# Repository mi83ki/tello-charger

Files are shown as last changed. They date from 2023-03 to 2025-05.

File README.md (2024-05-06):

<!-- omit in toc -->
# Tello Charger

小型ドローンTelloの自動充電を可能にする装置です。

<!-- omit in toc -->
## 目次

- [1. Tello Chargerとは](#1-tello-chargerとは)
- [2. 製作するために必要なデータ](#2-製作するために必要なデータ)
  - [2.1. 3Dデータ](#21-3dデータ)
  - [2.2. 回路図](#22-回路図)
  - [2.3. ソースコード](#23-ソースコード)
    - [2.3.1. 開発環境の構築](#231-開発環境の構築)
      - [2.3.1.1. VSCodeのインストール](#2311-vscodeのインストール)
      - [2.3.1.2. PlatformIOのインストール](#2312-platformioのインストール)
    - [2.3.2. 初期設定](#232-初期設定)
      - [2.3.2.1. サブモジュールの取得](#2321-サブモジュールの取得)
      - [2.3.2.2. ssid.hの作成](#2322-ssidhの作成)
    - [2.3.3. ソフトウェアの書き込み](#233-ソフトウェアの書き込み)
      - [2.3.3.1. ワークスペースを開く](#2331-ワークスペースを開く)
      - [2.3.3.2. ビルド](#2332-ビルド)
      - [2.3.3.3. 書き込み](#2333-書き込み)
- [3. WebAPI仕様](#3-webapi仕様)
- [4. 概要設計書](#4-概要設計書)

## 1. Tello Chargerとは

Tello EDUの自動充電装置です。

以下はドローンにUSBコネクタを接続する機構の動画です。

ドローンキャッチ (https://youtube.com/shorts/hyMHSOp_BFY)

以下はドローンを自動充電する一連動作の動画です。

ドローン着陸 (https://youtube.com/shorts/O7KXj6DnHRI)

## 2. 製作するために必要なデータ

製作するために必要なデータを以下に説明します。

### 2.1. 3Dデータ

3Dデータ（STEP）は`step/`ディレクトリに保存しています。\
STLデータ等に変換し、3Dプリンタで印刷します。\
3Dデータの品番リストは[概要設計書](doc/design/design.md)を参照してください。

### 2.2. 回路図

回路図（Eegleデータ）は`eagle/`ディレクトリに保存しています。\
必要な部品を購入し、ユニバーサル基板で手はんだします。\
必要な部品のリストは[概要設計書](doc/design/design.md)を参照してください。

### 2.3. ソースコード

ATOM Liteに書き込むソースコードは`src/`ディレクトリに保存しています。

#### 2.3.1. 開発環境の構築

##### 2.3.1.1. VSCodeのインストール

Arduinoマイコンへの書き込みも可能なエディタとしてVSCodeを推奨する。\
以下のURLに従ってVSCodeをインストールする。\
<https://miya-system-works.com/blog/detail/vscode-install/>

##### 2.3.1.2. PlatformIOのインストール

以下URLを参考に、VSCodeの拡張機能であるPlatformIOをインストールする。\
<https://zenn.dev/kotaproj/articles/esp32_vscode_pio>

#### 2.3.2. 初期設定

初回に必要な作業を記載します。

##### 2.3.2.1. サブモジュールの取得

以下のコマンドでサブモジュールを取得する必要があります。

~~~bash
git submodule update --init
~~~

##### 2.3.2.2. ssid.hの作成

WiFiの接続先SSIDとパスワードは以下の手順で設定します。

1. 「src/TelloCharger/src/」フォルダの「ssid_example.h」を同じフォルダにコピーして「ssid.h」に名称変更する

2. 「ssid.h」の各項目を自分の環境に合わせて変更する

    ~~~h
    /**
     * @file ssid_example.h
     * @brief SSID情報を記述するヘッダファイルの例
     *
     * @details 環境に合わせて、ファイル名をssid.hにリネームして利用してください（ssid.hはgitignoreされている）
     */

    #pragma once

    #define WIFI_SSID "XXXXXXXXXXX"
    #define WIFI_PASSWORD "XXXXXXXX"

    /** 固定IPアドレス（"MY_FIXED_IP_1"."MY_FIXED_IP_2"."MY_FIXED_IP_3"."MY_FIXED_IP_4"） */
    #define MY_FIXED_IP_1 (192)
    #define MY_FIXED_IP_2 (168)
    #define MY_FIXED_IP_3 (1)
    #define MY_FIXED_IP_4 (12)

    /** ゲートウェイのIPアドレス（"MY_FIXED_IP_1"."MY_FIXED_IP_2"."MY_FIXED_IP_3"."GATEWAY_IP_4"） */
    #define GATEWAY_IP_4 (1)
    ~~~

#### 2.3.3. ソフトウェアの書き込み

##### 2.3.3.1. ワークスペースを開く

「xsa-cloud/xsa-cloud.code-workspace」をダブルクリックしてVSCodeで開く。

##### 2.3.3.2. ビルド

左下の`✓`ボタンを押下する。

##### 2.3.3.3. 書き込み

クナイデバイスをUSBケーブルでPCに接続し、左下の`→`ボタンを押下する。

## 3. WebAPI仕様

TelloChargerは上位システムからWebAPIで制御します。\
以下のAPI仕様を参照してください。

[Tello Charger API](doc/openapi/api.html)

## 4. 概要設計書

概要設計内容は以下を参照してください。

[概要設計書](doc/design/design.md)

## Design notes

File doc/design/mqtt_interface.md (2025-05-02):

<!-- omit in toc -->
# MQTT通信仕様書

<!-- omit in toc -->
## 改訂履歴

| 日付 | 版 | 変更者 | 変更内容 |
|---|----|---|---|
| 2025/5/2 | 0.1.0 | Miyazaki | 初版作成 |

<!-- omit in toc -->
## 目次

- [1. 目的](#1-目的)
- [2. システム全体概要](#2-システム全体概要)
- [3. ブローカー設定](#3-ブローカー設定)
- [4. トピック定義](#4-トピック定義)
- [5. ペイロード仕様](#5-ペイロード仕様)
  - [5.1. 共通ヘッダー (要求/応答系)](#51-共通ヘッダー-要求応答系)
  - [5.2. `ChargeStatusPayload`](#52-chargestatuspayload)
  - [5.3. `ChargeStartRequestPayload`](#53-chargestartrequestpayload)
  - [5.4. `ChargeStartResponsePayload`](#54-chargestartresponsepayload)
  - [5.5. `ChargeStopRequestPayload`](#55-chargestoprequestpayload)
  - [5.6. `ChargeStopResponsePayload`](#56-chargestopresponsepayload)
  - [5.7. `PowerOnRequestPayload`](#57-poweronrequestpayload)
  - [5.8. `PowerOnResponsePayload`](#58-poweronresponsepayload)

---

## 1. 目的

このドキュメントは、システム内で使用する **MQTT 通信** の仕様を統一し、開発者・運用者間で共通理解を得ることを目的とします。

---

## 2. システム全体概要

MQTT

---

## 3. ブローカー設定

| 項目 | 値 | 備考 |
|---|----|---|
| ホスト名 | `XX.XX.XX.XX` | MQTTブローカーのホスト |
| ポート | `1883` | — |
| プロトコル | MQTT v3.1 | — |

---

## 4. トピック定義

> `{device_id}` は実際のデバイス ID に置換して利用してください。

| トピック | 方向<br>(Pub/Sub) | QoS | Retain | Payloadスキーマ | 説明 |
|---|:---:|:---:|:---:|---|---|
| `drone-charger/{device_id}/charge/status` | Pub | 1 | No | `ChargeStatusPayload` | 充電状態の定期通知 |
| `drone-charger/{device_id}/charge/start/request` | Sub | 1 | No | `ChargeStartRequestPayload` | 充電開始要求 |
| `drone-charger/{device_id}/charge/start/response` | Pub | 1 | No | `ChargeStartResponsePayload` | 充電開始応答 |
| `drone-charger/{device_id}/charge/stop/request` | Sub | 1 | No | `ChargeStopRequestPayload` | 充電停止要求 |
| `drone-charger/{device_id}/charge/stop/response` | Pub | 1 | No | `ChargeStopResponsePayload` | 充電停止応答 |
| `drone-charger/{device_id}/power/on/request` | Sub | 1 | No | `PowerOnRequestPayload` | 電源ON要求 |
| `drone-charger/{device_id}/power/on/response` | Pub | 1 | No | `PowerOnResponsePayload` | 電源ON応答 |

---

## 5. ペイロード仕様

### 5.1. 共通ヘッダー (要求/応答系)

| フィールド | 型 | 必須 | 説明 |
|---|----|:----:|---|
| `timestamp` | string (ISO 8601) | Yes | 送信日時 (UTC) |
| `req_id` | string (UUIDv4) | Yes | 要求一意識別子 |
| `status` | string | Yes | 処理結果 (`SUCCESS`, `FAILURE` など) |
| `error` | string | No | エラー詳細 (成功時は空文字) |

### 5.2. `ChargeStatusPayload`

```json
{
  "charge": true,
  "current": 0,
  "chargingTime": 0,
  "isStartChargeExecuting": true,
  "isStopChargeExecuting": true,
  "isPowerOnExecuting": true
}
```

| フィールド | 型 | 必須 | 説明 |
|---|----|:----:|---|
| `charge` | boolean | Yes | 充電中かどうか (`true` = 充電中) |
| `current` | number | Yes | 充電電流 (mA) |
| `chargingTime` | number | Yes | 充電経過時間 (秒) |
| `isStartChargeExecuting` | boolean | Yes | 充電開始処理が実行中か |
| `isStopChargeExecuting` | boolean | Yes | 充電停止処理が実行中か |
| `isPowerOnExecuting` | boolean | Yes | 電源ON処理が実行中か |

### 5.3. `ChargeStartRequestPayload`

```json
{
  "timestamp": "2025-05-02T11:00:00Z",
  "req_id": "550e8400-e29b-41d4-a716-446655440000"
}
```

### 5.4. `ChargeStartResponsePayload`

```json
{
  "req_id": "550e8400-e29b-41d4-a716-446655440000",
  "status": "SUCCESS",
  "error": ""
}
```

### 5.5. `ChargeStopRequestPayload`

```json
{
  "timestamp": "2025-05-02T11:05:00Z",
  "req_id": "3fa85f64-5717-4562-b3fc-2c963f66afa6"
}
```

### 5.6. `ChargeStopResponsePayload`

```json
{
  "req_id": "3fa85f64-5717-4562-b3fc-2c963f66afa6",
  "status": "SUCCESS",
  "error": ""
}
```

### 5.7. `PowerOnRequestPayload`

```json
{
  "timestamp": "2025-05-02T11:10:00Z",
  "req_id": "1c16f6e0-6737-4d62-8c06-9f9fbc2384d8"
}
```

### 5.8. `PowerOnResponsePayload`

```json
{
  "req_id": "1c16f6e0-6737-4d62-8c06-9f9fbc2384d8",
  "status": "SUCCESS",
  "error": ""
}
```

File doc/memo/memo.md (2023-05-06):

<!-- omit in toc -->
# ドローン制御システム自由研究

## 1. 自動充電

### 1.1. Fusion360で平歯車の作成

ツール⇒アドイン⇒スクリプトとアドイン⇒Spur Gear（下側）
https://www.fact-cam.co.jp/product/2019/10/fusion360/archives/000447.html

## 2. GPS

### 2.1. telloにtileを付けた事例

https://www.thingiverse.com/thing:2943670
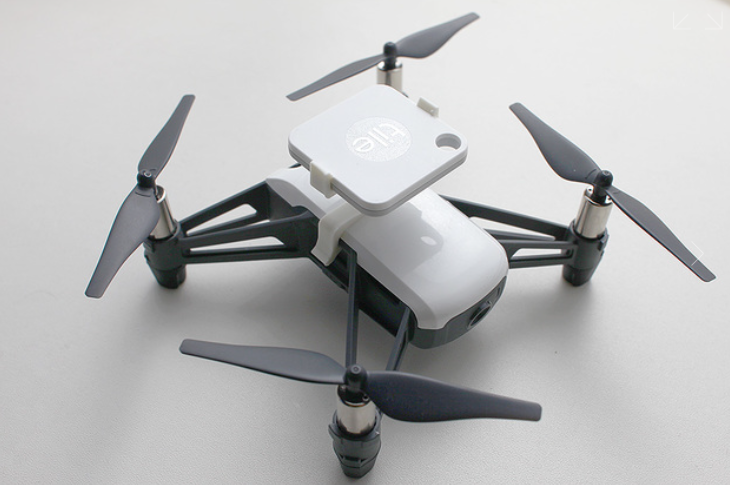
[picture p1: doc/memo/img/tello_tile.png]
tello_tile


## 3. センサ追加

| 品名 | 価格 | URL |
| --- | ---- | --- |
| TVOC/eCO2 ガスセンサユニット（SGP30） | 1606 | https://www.switch-science.com/products/6619 |
| M5Stack用 温湿度CO2センサ（SCD41） | 7117 | https://www.switch-science.com/products/8668 |
| ATOM Motionキット モーター/サーボドライバ（STM32F0搭載） | 3553 | https://www.switch-science.com/products/6993 |
| ATOMS3 Lite | 1386 | https://www.switch-science.com/products/8778 |

## 4. PlatformIOを使ってみる

### 4.1. PlatformIOのインストール

以下のURLを参考にPlatformIOをインストールします。\
<https://takabus.com/tips/2402/>

1. VSCodeをインストールする
1. PlatformIOの拡張機能をインストールする
1. プロジェクトを新規作成する
1. 今回はATOM Liteを使用するため、Bord: M5Stack-ATOM を選択する

### 4.2. ライブラリのインストール

PlatformIOのLibrariesから以下をインストールする

1. M5Atom
1. FastLED

## 5. サンプルプログラムの実行

以下のLチカプログラムを実行する

~~~cpp
#include <M5Atom.h> //Atomのヘッダファイルを準備
//FastLED（CRGB構造体）設定
CRGB dispColor(uint8_t r, uint8_t g, uint8_t b) {
  return (CRGB)((r << 16) | (g << 8) | b);
}
// 初期設定 -----------------------------------------------
void setup() {
  // 本体初期化（UART有効, I2C無効, LED有効
  M5.begin(true, false, true);
  // LED全消灯（赤, 緑, 青)
  M5.dis.drawpix(0, dispColor(0, 0, 0));
}
// メイン -------------------------------------------------
void loop() {
  M5.update(); //本体のボタン状態更新
  if (M5.Btn.isPressed()) {  //ボタンが押されていれば
    M5.dis.drawpix(0, dispColor(0, 0, 255)); //LED（指定色）
  } else { //ボタンが押されてなければ
    M5.dis.drawpix(0, dispColor(20, 20, 20)); //LED（白）
  }
  delay(100); //100ms待機
}
~~~

## 6. 自作ライブラリの取り込み

~~~bash
cd src/TelloCharger/lib/
git submodule add https://github.com/mi83ki/ArduinoCommon.git
~~~

## 7. WebAPIサーバーにする

参考にしたURL
<https://qiita.com/poruruba/items/0e539875ecfbdbfb23db>

### 7.1. ライブラリのインストール

以下のライブラリインストールする

- bblanchon/ArduinoJson@^6.21.2
- ottowinter/ESPAsyncWebServer-esphome@^3.0.0

### 7.2. サンプルプログラムの実行

~~~cpp
#include <ArduinoJson.h>
#include <AsyncJson.h>
#include <AsyncTCP.h>
#include <ESPAsyncWebServer.h>
#include <M5Atom.h>

const char *wifi_ssid = "Your SSID";
const char *wifi_password = "Your Password";

#define HTTP_PORT 80
#define FORMAT_SPIFFS_IF_FAILED true
#define BUFFER_SIZE 30 * 1024
unsigned char buffer[BUFFER_SIZE];

AsyncWebServer server(HTTP_PORT);

void wifi_connect(const char *ssid, const char *password);

void notFound(AsyncWebServerRequest *request) {
  if (request->method() == HTTP_OPTIONS) {
    request->send(200);
  } else {
    request->send(404);
  }
}

void setup() {
  Serial.begin(115200);

  wifi_connect(wifi_ssid, wifi_password);

  server.on("/get", HTTP_GET, [](AsyncWebServerRequest *request) {
    AsyncWebParameter *p = request->getParam("download");
    if (p != NULL)
      Serial.println(p->value());

    request->send(200, "text/plain", "Hello, world");
  });

  AsyncCallbackJsonWebHandler *handler = new AsyncCallbackJsonWebHandler(
      "/post", [](AsyncWebServerRequest *request, JsonVariant &json) {
        JsonObject jsonObj = json.as<JsonObject>();
        int p1 = jsonObj["p1"] | -1;

        const char *p_param = jsonObj["param"];
        if (p_param != NULL) {
          Serial.println(p_param);
        }

        //    request->send(200, "application/json", "{}");
        AsyncJsonResponse *response = new AsyncJsonResponse();
        JsonObject root = response->getRoot();
        root["p1"] = p1;
        root["message"] = "Hello World";
        response->setLength();
        request->send(response);
      });
  server.addHandler(handler);

  server.onNotFound(notFound);

  DefaultHeaders::Instance().addHeader("Access-Control-Allow-Origin", "*");
  DefaultHeaders::Instance().addHeader("Access-Control-Allow-Headers", "*");
  server.begin();
}

void loop() {
  // put your main code here, to run repeatedly:
}

void wifi_connect(const char *ssid, const char *password) {
  Serial.println("");
  Serial.print("WiFi Connenting");

  WiFi.begin(ssid, password);
  while (WiFi.status() != WL_CONNECTED) {
    Serial.print(".");
    delay(1000);
  }

  Serial.println("");
  Serial.print("Connected : ");
  Serial.println(WiFi.localIP());
}
~~~

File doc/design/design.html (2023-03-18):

# Tello Charger 設計

Tello Chargerの設計について記載する。

## 目次

- Telloとは
- 1. 要件定義
  - 1.1. ユースケース図
- 2. 機構設計
  - 2.1. アイデアスケッチ
  - 2.2. 3DCAD設計
- 電気設計
  - 回路ブロック図
- ソフト設計

## Telloとは

Telloとは、Ryze Tech社が販売している100g以下のトイドローン。
ここでは、SDKが公開されているTello EDUを自動充電するための装置を開発する。
Tello EDU: https://www.ryzerobotics.com/jp/tello-edu

## 1. 要件定義

### 1.1. ユースケース図

## 2. 機構設計

### 2.1. アイデアスケッチ

開始当初の自動充電構想。
着陸後、中心に寄せて充電プラグを接続するイメージ。

ドローンの位置を中央に寄せる機構と、自動充電プラグを接続する機構のイメージ。
RCサーボ2軸で簡単に実現したい。

### 2.2. 3DCAD設計

3DCADにて詳細設計。
3Dプリンタで印刷する。

## 電気設計

### 回路ブロック図

回路ブロック図は以下になります。

## ソフト設計

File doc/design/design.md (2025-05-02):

<!-- omit in toc -->
# Tello Charger 概要設計書

Tello Chargerの概要設計について記載します。

<!-- omit in toc -->
## 目次

- [1. Telloとは](#1-telloとは)
- [2. 要件定義](#2-要件定義)
  - [2.1. ユースケース図](#21-ユースケース図)
- [3. 機構設計](#3-機構設計)
  - [3.1. アイデアスケッチ](#31-アイデアスケッチ)
  - [3.2. 3DCAD設計](#32-3dcad設計)
- [4. 電気設計](#4-電気設計)
  - [4.1. 回路ブロック図](#41-回路ブロック図)
  - [4.2. 回路図](#42-回路図)
  - [4.3. 基板レイアウト](#43-基板レイアウト)
  - [4.4. 主要部品リスト](#44-主要部品リスト)
- [5. ソフト設計](#5-ソフト設計)
  - [5.1. コンテキスト図](#51-コンテキスト図)
  - [5.2. データフロー図](#52-データフロー図)
  - [5.3. モジュール構造図](#53-モジュール構造図)
  - [5.4. WebAPI仕様](#54-webapi仕様)
  - [MQTT通信仕様](#mqtt通信仕様)

## 1. Telloとは

Telloとは、Ryze Tech社が販売している100g以下のトイドローンです。\
ここでは、SDKが公開されているTello EDUを自動充電するための装置を開発します。\
Tello EDU: <https://www.ryzerobotics.com/jp/tello-edu>

## 2. 要件定義

TelloChargerで実現したい要件を定義します。

### 2.1. ユースケース図

以下のユースケースを実現します。

usecase

## 3. 機構設計

機構設計について記載します。

### 3.1. アイデアスケッチ

開始当初の自動充電構想です。\
着陸後、中心に寄せて充電プラグを接続するイメージです。

ideaSketch

ドローンの位置を中央に寄せる機構と、自動充電プラグを接続する機構のイメージです。\
RCサーボ2軸で簡単に実現する機構にします。

ideaSketch

### 3.2. 3DCAD設計

3DCADにて詳細設計を行い、3Dプリンタで印刷します。

mechaDesign

アセンブリのSTEPデータは`step/`ディレクトリに保存しています。\
以下は3Dデータに含まれる部品の品番リストです。

| 品番 | 品名（日本語） | 品名（英語） | 員数 | 備考 |
| --- | --- | --- | ---- | --- |
| AILAB21P0001 | メインケース | MainCase | 1 | |
| AILAB21P0002 | カバーA | CoverA | 2 | |
| AILAB21P0003 | カバーB | CoverB | 4 | |
| AILAB21P0004 | カバーC | CoverC | 4 | |
| AILAB21P0006 | サブケース | SubCase | 1 | |
| AILAB21P0007 | アームA | ArmA | 1 | |
| AILAB21P0008 | アームB | ArmB | 1 | |
| AILAB21P0009 | アームC | ArmC | 1 | |
| AILAB21P0010 | スライドレール | SlideRail | 1 | |
| AILAB21P0011 | リンク | Link | 1 | |
| xmec_PT2.6x12-B | バインドPタイト2.6x12mm | - | 4 | |
| xmec_PT2.6x8-B  | バインドPタイト2.6x8mm  | - | 16 | |
| xmec_PT2.0x6-B  | バインドPタイト2.0x6mm  | - | 6 | |
| xmec_M3x8-N | M3なべ小ねじx8mm | - | 8 | |
| xmec_NUT-M3 | M3ナット | - | 8 | |
| xmec_takegushi  | 竹串 | - | 44 | 着陸ガイドには竹串を使用 |
| xele_cable | マグネットUSBケーブル | - | 1 | [購入リンク](https://www.amazon.co.jp/gp/product/B07GQVHP67/ref=ppx_yo_dt_b_asin_title_o04_s00?ie=UTF8&th=1) |

## 4. 電気設計

電気設計について記載します。

### 4.1. 回路ブロック図

回路ブロック図は以下になります。

- マイコンはATOM Liteを採用
- 以下2点の目的で電流センサを搭載する
  - 充電電流を監視し、充電状態を取得する
  - サーボ電流を監視し、過負荷を検知する
- 充電電圧をMOSFETで制御（Telloの電源を入れる目的）

blockDiagram

### 4.2. 回路図

回路図を以下に示します。\
Eagleの設計データは`eagle/`ディレクトリに保存しています。

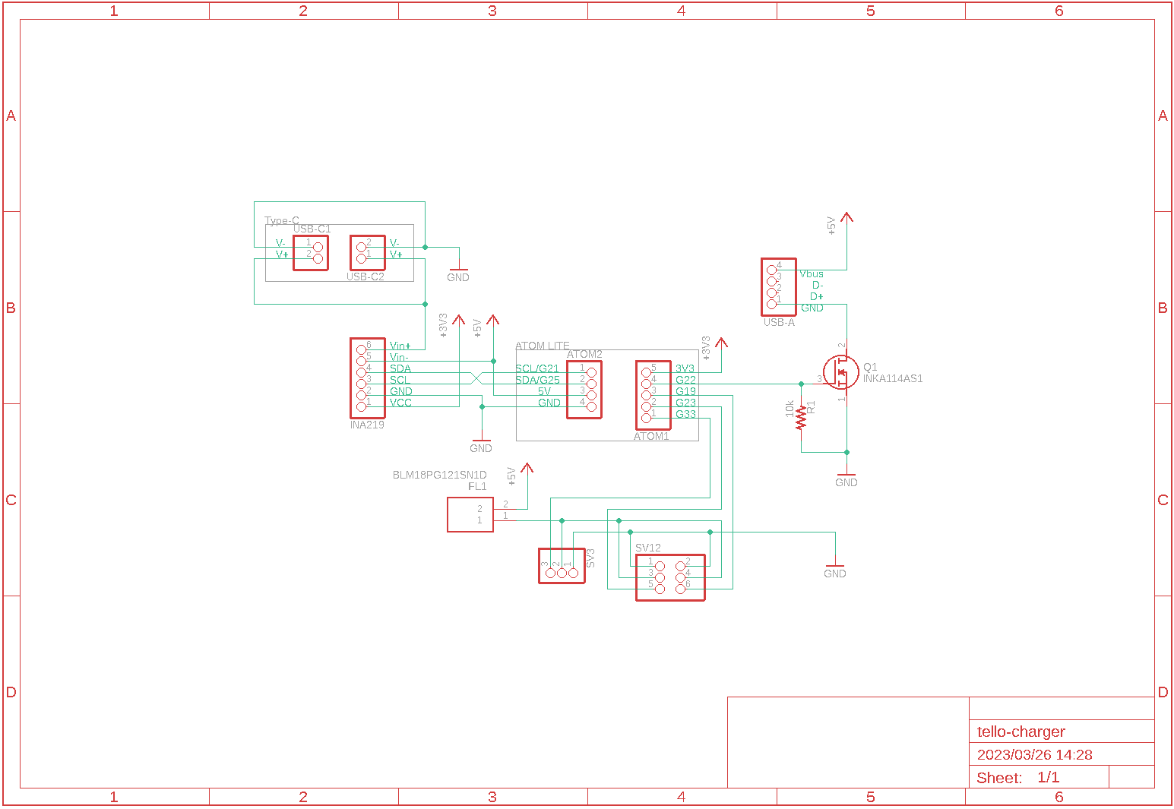
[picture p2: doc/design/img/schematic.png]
schematic


### 4.3. 基板レイアウト

部品の配置図を示します。
pcbLayout

### 4.4. 主要部品リスト

主要部品のリストを以下に示します。

| No. | 品名 | 型番 | 個数 | 参考URL |
| --- | --- | --- | ---- | --- |
| 1 | ATOM Lite | ATOM Lite | 1 | <https://www.switch-science.com/products/6262>  |
| 2 | RCサーボ | GWSMIRMGFA | 2 | <https://akizukidenshi.com/catalog/g/gM-01908/> |
| 3 | 電流センサ | INA219使用電流センサーモジュール | 1 | <https://akizukidenshi.com/catalog/g/gM-08221/> |
| 4 | USB-A DIP化 | AE-USB-A-DIP | 1 | <https://akizukidenshi.com/catalog/g/gK-07429/> |
| 5 | USB-C DIP化 | AE-USB2.0-TYPE-C-CTRPB-1 | 1 | <https://akizukidenshi.com/catalog/g/gK-17123/> |
| 6 | Nch MOSFET | 2SK4017(Q) | 1 | <https://akizukidenshi.com/catalog/g/gI-07597/> |
| 7 | フェライトビーズ  | BLM18RK121SN1D | 1 | <https://akizukidenshi.com/catalog/g/gP-04445/> |
| 8 | チップ抵抗 | 1608 10kΩ | 1 | |
| 9 | ピンヘッダ 1x5 | PH-1x40SG | 1 | <https://akizukidenshi.com/catalog/g/gC-00167/> |
| 9 | ピンヘッダ 1x4 | PH-1x40SG | 1 | <https://akizukidenshi.com/catalog/g/gC-00167/> |
| 9 | ピンヘッダL型 2x3 | PH-2x10RG | 1 | <https://akizukidenshi.com/catalog/g/gC-10903/> |
| 10  | ピンソケット 1x6  | FH-1x6SG/RH | 適量 | <https://akizukidenshi.com/catalog/g/gC-03784/> |

## 5. ソフト設計

ATOM Liteに書き込むファームウェアの設計内容を記載します。

### 5.1. コンテキスト図

以下にコンテキスト図を記載します。

Context Diagram

### 5.2. データフロー図

以下にデータフロー図を記載します。

Dataflow Diagram

### 5.3. モジュール構造図

以下にモジュール構造図を記載します。

Module Structure

### 5.4. WebAPI仕様

TelloChargerは上位システムからの充電指示をWebAPIで受け付けるようにします。\
以下にWebAPI仕様を記載します。

[Tello Charger API](../openapi/api.html)

### MQTT通信仕様

MQTT brokerを経由して通信することも可能です。\
以下にMQTT通信仕様を記載します。

[MQTT通信仕様](mqtt_interface.md)

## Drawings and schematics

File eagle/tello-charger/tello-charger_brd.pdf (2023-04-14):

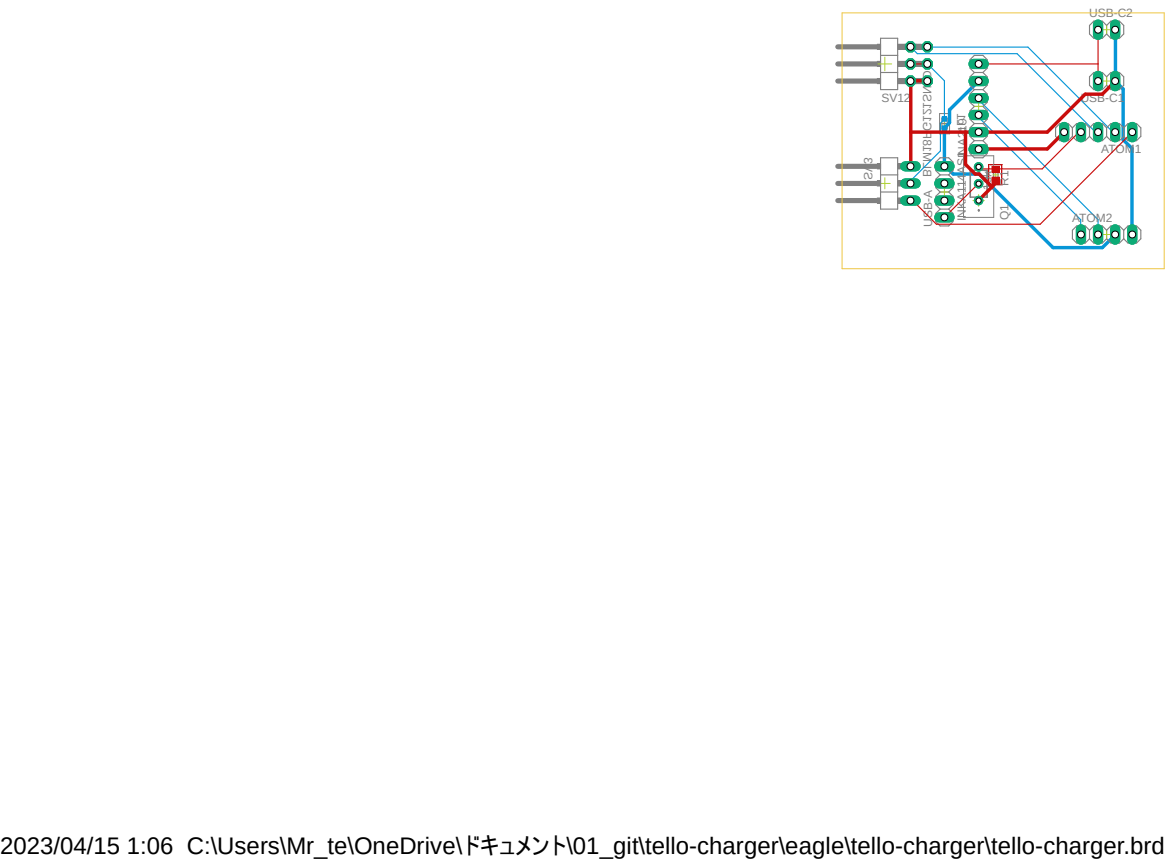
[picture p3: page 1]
2023/04/15 1:06 C:\Users\Mr_te\OneDrive\ドキュメント\01_git\tello-charger\eagle\tello-charger\tello-charger.brd SV³; BLM¹⁸PG¹²¹SN¹D; ATOM1; ATOM2 INA²¹⁹; Q¹ R¹ USB⁻A; USB-C1; USB-C2; INKA¹¹⁴AS¹

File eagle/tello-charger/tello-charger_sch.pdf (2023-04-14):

A

A

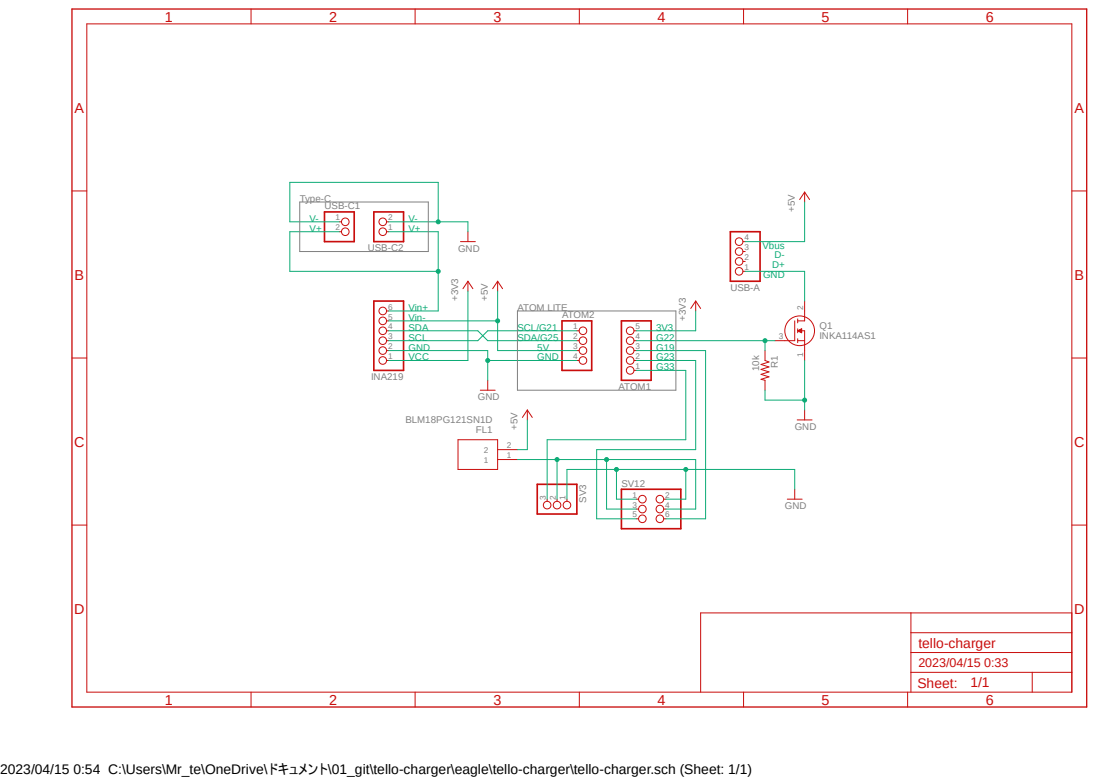
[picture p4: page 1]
INKA114AS1 ⁺⁵V; GND ⁺³V³; GND; GND ¹⁰k +3V³ +5V; BLM18PG121SN1D; 5 ATOM1; 4 ATOM2; 4 USB-A; 2 USB-C1; 2 USB-C2; 6 INA219; Sheet:; tello-charger; SCL/G21; Vin+ Vin- SDA SCL GND VCC; Vbus; ATOM LITE; Type-C

SDA/G25 | 2
5V | 3

2023/04/15 0:54 C:\Users\Mr_te\OneDrive\ドキュメント\01_git\tello-charger\eagle\tello-charger\tello-charger.sch (Sheet: 1/1)

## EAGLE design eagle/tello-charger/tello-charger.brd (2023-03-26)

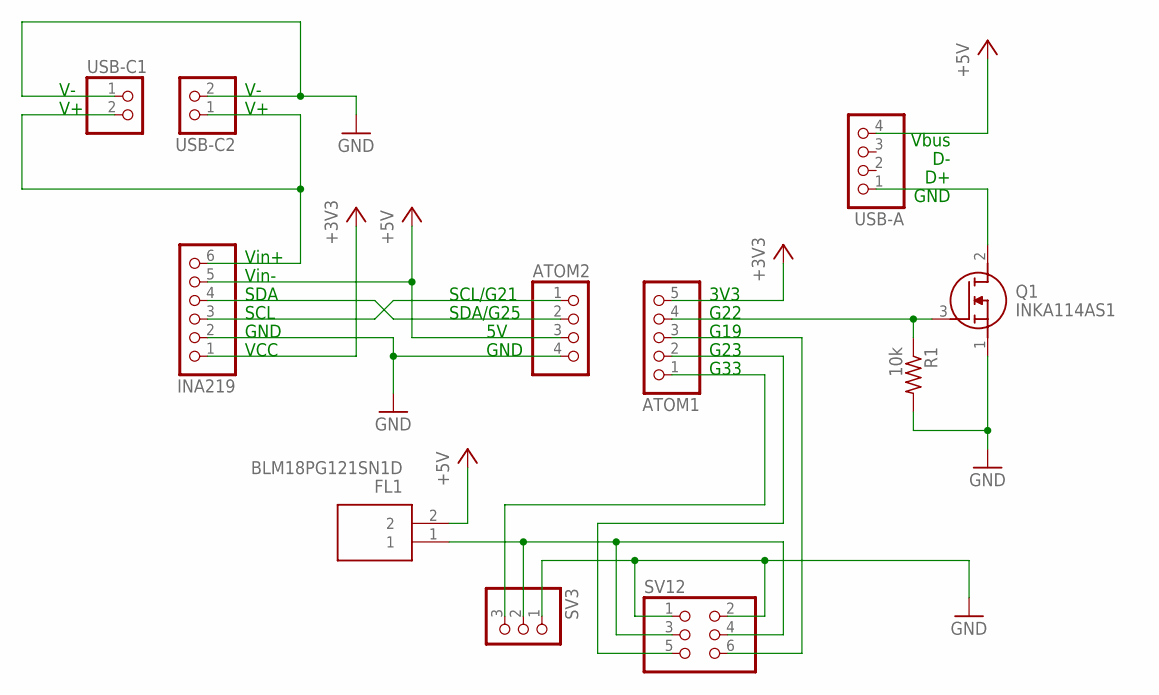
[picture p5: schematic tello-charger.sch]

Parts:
ATOM1: PINHD-1X5; 1X05
ATOM2: PINHD-1X4; 1X04
FL1: BLM18PG121SN1D; BLM18AG102BH1D
INA219: PINHD-1X6; 1X06
Q1: INKA114AS1
R1: 10k; R0603
SV3: PINHD-1X3/90; 1X03/90
SV12: PINHD-2X3/90; 2X03/90
USB-A: PINHD-1X4; 1X04
USB-C1, USB-C2: PINHD-1X2; 1X02

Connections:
+3V3: ATOM1.5, INA219.1
+5V: ATOM2.3, FL1.2, INA219.5, USB-A.4
GND: ATOM2.4, INA219.2, Q1.1 (S), R1.2, SV3.1, SV12.1, SV12.2, USB-C1.1, USB-C2.2
unnamed: INA219.6, USB-C1.2, USB-C2.1
unnamed: Q1.2 (D), USB-A.1
unnamed: ATOM2.2, INA219.4
unnamed: ATOM2.1, INA219.3
unnamed: ATOM1.2, SV12.5
unnamed: ATOM1.4, Q1.3 (G), R1.1
unnamed: FL1.1, SV3.2, SV12.3, SV12.4
unnamed: ATOM1.3, SV12.6
unnamed: ATOM1.1, SV3.3

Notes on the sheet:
3V3
G22
G19
G23
G33
SCL/G21
SDA/G25
GND
Vin+
Vin-
SDA
SCL
VCC
Vbus

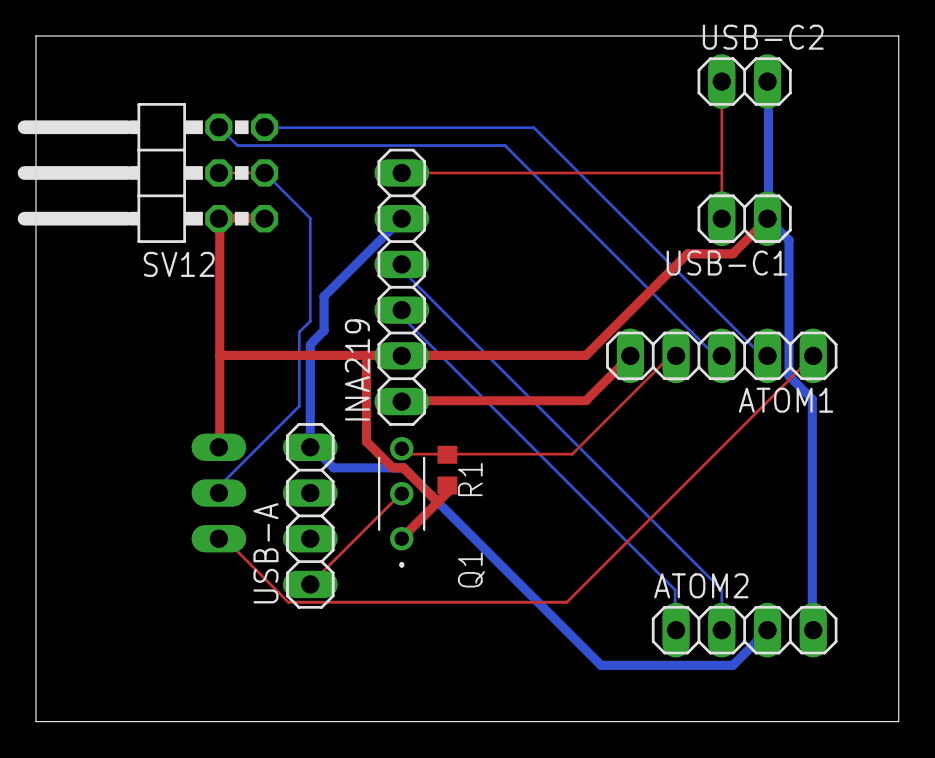
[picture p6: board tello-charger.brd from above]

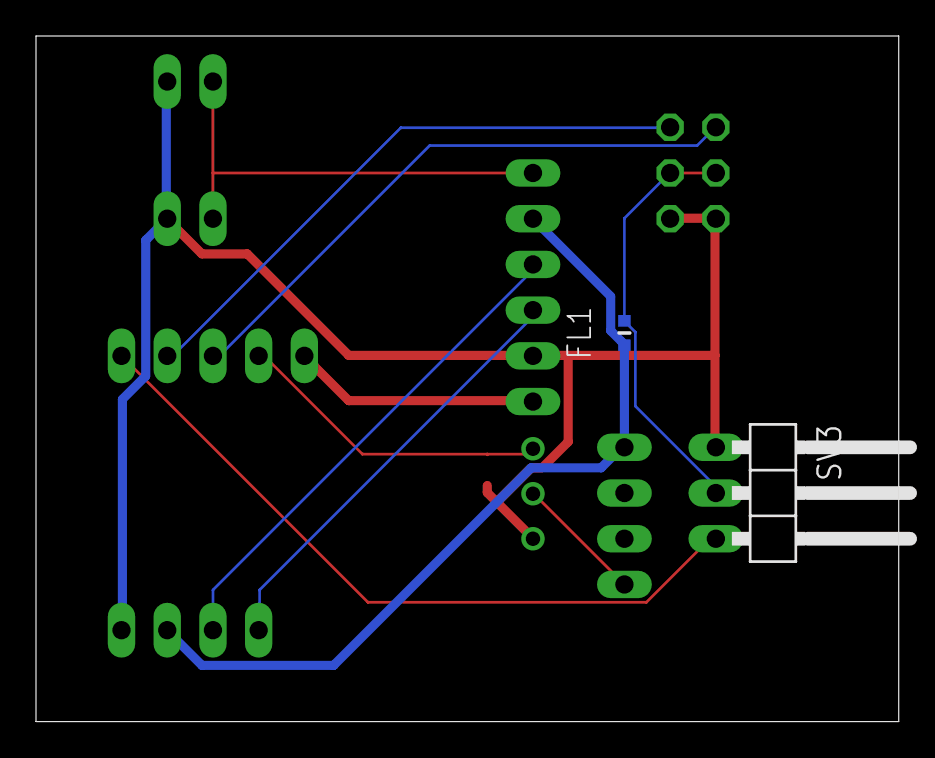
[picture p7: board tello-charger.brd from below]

Board: 2 copper layers, 47.9 x 38.1 mm, 11 parts (2 on the bottom side), 12 nets.

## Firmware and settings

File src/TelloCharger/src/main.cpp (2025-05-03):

#include <Log.h>
#include <M5Unified.h>
#include <MQTTClientESP32.h>
#include <MacUtils.h>
#include <WiFiESP32.h>

#include "ChargeController/ChargeController.h"
#include "HttpServer/DroneChargerProtocol.h"
#include "HttpServer/HttpServer.h"
#include "HttpServer/MqttHandler.h"
#include "ssid.h"

/** WiFiのSSID（ssid.h（git管理対象外）にて定義） */
const char *wifiSSID = WIFI_SSID;
/** WiFiのパスワード（ssid.h（git管理対象外）にて定義） */
const char *wifiPassword = WIFI_PASSWORD;
/** WebAPIの待ち受けポート */
const uint8_t httpPort = 80;

/** WiFi接続インスタンス */
WiFiESP32 *wifi;
/** MQTTクライアントインスタンス */
MQTTClientESP32 *mqttClient;
/** MQTTハンドラインスタンス */
MqttHandler *mqttHandler;
/** WebAPIインスタンス */
HttpServer *server;
/** 充電制御インスタンス */
ChargeController *charger;

/**
 * @brief WiFi通信用Task
 */
void taskWifi(void *) {
  wifi = new WiFiESP32(wifiSSID, wifiPassword);

  // for fixed IP Address
  IPAddress ip(MY_FIXED_IP_1, MY_FIXED_IP_2, MY_FIXED_IP_3, MY_FIXED_IP_4);
  IPAddress gateway(MY_FIXED_IP_1, MY_FIXED_IP_2, MY_FIXED_IP_3, GATEWAY_IP_4);
  IPAddress subnet(255, 255, 255, 0);
  WiFi.config(ip, gateway, subnet);

  // WiFi接続
  if (!wifi->begin()) {
    logger.info("WiFi Init Fail");
    // ESP.restart();
  }

  server = new HttpServer(httpPort, charger);
  mqttClient = new MQTTClientESP32(MQTT_HOST, MQTT_PORT, MQTT_BUFFER_SIZE);
  mqttHandler = new MqttHandler(mqttClient, charger, DEFAULT_MAC_ADDRESS);

  while (true) {
    if (wifi->healthCheck()) {
      server->begin();
      mqttHandler->loop();
    } else {
      server->end();
    }
    vTaskDelay(1);
  }
}

void setup() {
  auto cfg = M5.config();
  M5.begin(cfg);
  charger = new ChargeController();
  // WiFi通信用Taskを起動 Core 0
  xTaskCreatePinnedToCore(taskWifi, "taskWifi", 4096, NULL, 1, NULL, 0);
}

void loop() {
  // ボタン押下時の処理
  M5.update();
  if (M5.BtnA.wasPressed()) {
    if (charger->isReleaseDrone())
      charger->startCharge();
    else
      charger->stopCharge();
  }

  // キーボードからのWASD入力時の処理
  if (Serial.available()) {
    // 文字が届いていればを読み込む
    char input = Serial.read();
    charger->wasdControl(input);
  }

  // 制御部のループ処理
  charger->loop();
  delay(10);
}

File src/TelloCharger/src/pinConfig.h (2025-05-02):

// build_flags で与えた名前
#ifdef M5STACK_M5ATOMS3
// Atom S3 系
/** 捕獲サーボのピン番号 */
#define SERVO_CATCH_PIN 6
/** USBサーボのピン番号 */
#define SERVO_USB_PIN 7
/** MOSFETのピン番号 */
#define CHARGE_CONTROL_PIN 5
#define INA_SDA_PIN 38
#define INA_SCL_PIN 39
#else
// Atom 系
/** 捕獲サーボのピン番号 */
#define SERVO_CATCH_PIN 19
/** USBサーボのピン番号 */
#define SERVO_USB_PIN 23
/** MOSFETのピン番号 */
#define CHARGE_CONTROL_PIN 22
#define INA_SDA_PIN 25
#define INA_SCL_PIN 21
#endif

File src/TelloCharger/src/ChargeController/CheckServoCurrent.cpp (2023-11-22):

/**
 * @file CheckServoCurrent.cpp
 * @brief サーボ電流を監視するクラス
 * @author Tatsuya Miyazaki
 * @date 2023/11/20
 *
 * @details サーボ電流を監視するクラス
 */

#include "CheckServoCurrent.h"

#include <Log.h>

/**
 * @brief Construct a new Check Servo Current:: Check Servo Current object
 *
 * @param servo
 * @param fet
 * @param current
 */
CheckServoCurrent::CheckServoCurrent(ServoController *servo, FETController *fet,
                                     CurrentReader *current)
    : ControlBase(servo, fet, current, "CheckServoCurrent"),
      _isServoMovingPrevious(false),
      _haveToEmargencyStopServo(false) {}

// この電流[mA]より大きければサーボモータ稼働中
const float CheckServoCurrent::SERVO_CURRENT_MOVING_THREASHOLD = 150.0;
// 以下の時間過電流を検知すればサーボを止める
const uint32_t CheckServoCurrent::SERVO_MOVING_TIMEOUT = 5000;

/**
 * @brief
 *
 * @return true
 * @return false
 */
bool CheckServoCurrent::isServoOverCurrent(void) {
  return !_fet->read() && _servo->isTargetAngle() &&
         isServoMoving(_current->getCurrent());
}

/**
 * @brief 非常停止が必要かどうか
 *
 * @return true
 * @return false
 */
bool CheckServoCurrent::haveToEmargencyStopServo(void) {
  if (_haveToEmargencyStopServo) {
    _haveToEmargencyStopServo = false;
    return true;
  }
  return false;
}

/**
 * @brief アームを初期位置に戻すループ処理
 *
 * @return true 処理完了
 * @return false 処理中
 */
bool CheckServoCurrent::loop(void) {
  static Timer timer = Timer(500);
  if (timer.isCycleTime()) {
    logger.debug(
        "checkServoTimeout(): current = " + String(_current->getCurrent()) +
        ", isMoving = " + String(isServoOverCurrent()));
  }
  switch (_step) {
    case 0:
      if (isServoOverCurrent()) {
        // サーボ指示値が収束した状態で過電流を検知した
        _timer.startTimer();
        _step++;
        logger.debug("checkServoTimeout(): start timer");
      }
      break;
    case 1:
      if (isServoOverCurrent() && _timer.getTime() >= SERVO_MOVING_TIMEOUT) {
        // 過電流がタイムアウトした場合
        logger.error("checkServoTimeout(): servo moving timeout. time = " +
                     String(_timer.getTime()) +
                     ", current = " + String(_current->getCurrent()));
        _haveToEmargencyStopServo = true;
        if (_servo->isCatchDrone())
          _step = 10;
        else
          _step = 20;
      } else if (!isServoOverCurrent()) {
        // サーボの稼働が終了した
        logger.debug("checkServoTimeout(): finish servo moving. time = " +
                     String(_timer.getTime()) +
                     ", current = " + String(_current->getCurrent()));
        _step = 99;
      }
      break;
    case 10:
      // 非常停止処理（アームを開く）
      if (_servo->isConnectUsb()) {
        // まずはUSBアームを動かす
        _servo->disconnectUsb();
        logger.info("emargencyStopServo(): Set USB servo angle from " +
                    String(_servo->servoUsb()->getPresentAngle()) + " to " +
                    String(_servo->servoUsb()->getTargetAngle()));
      } else if (_servo->isDisconnectUsb()) {
        // USBアームが閉じてから捕獲アームを動かす
        _servo->releaseDrone();
        logger.info("emargencyStopServo(): Set Catch servo angle from " +
                    String(_servo->servoCatch()->getPresentAngle()) + " to " +
                    String(_servo->servoCatch()->getTargetAngle()));
        _step = 99;
      }
      break;
    case 20:
      // 非常停止処理（アームを閉じる）
      if (_servo->isReleaseDrone()) {
        // まずは捕獲アームを動かす
        _servo->catchDrone();
        logger.info("emargencyStopServo(): Set Catch servo angle from " +
                    String(_servo->servoCatch()->getPresentAngle()) + " to " +
                    String(_servo->servoCatch()->getTargetAngle()));
      } else if (_servo->isCatchDrone()) {
        // 捕獲アームが閉じてからUSBアームを動かす
        _servo->connectUsb();
        logger.info("emargencyStopServo(): Set USB servo angle from " +
                    String(_servo->servoUsb()->getPresentAngle()) + " to " +
                    String(_servo->servoUsb()->getTargetAngle()));
        _step = 99;
      }
      break;
    default:
      _step = 0;
      return true;
  }
  return false;
}

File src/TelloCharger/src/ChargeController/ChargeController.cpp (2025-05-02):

/**
 * @file ChargeController.cpp
 * @brief 充電制御クラス
 * @author Tatsuya Miyazaki
 * @date 2023/5/5
 *
 * @details サーボモータとMOSFETを制御するクラス
 */

#include "ChargeController.h"
#include "pinConfig.h"

#include <Log.h>

// この電流[mA]より大きければ充電中
const float ChargeController::CHARGE_CURRENT_CHARGING_THREASHOLD = 100.0;
// この電流[mA]より小さくなると充電を終了する
const float ChargeController::CHARGE_CURRENT_STOP_THREASHOLD = 200.0;

/**
 * @brief Construct a new Servo Controller:: Servo Controller object
 *
 */
ChargeController::ChargeController()
    : _servo(ServoController(SERVO_CATCH_PIN, SERVO_USB_PIN)),
      _fet(FETController(CHARGE_CONTROL_PIN)),
      _current(CurrentReader(200)),
      _chargeTimer(Timer()),
      _controlStartCharge(
          ControlStartCharge(&_servo, &_fet, &_current, &_chargeTimer)),
      _controlStopCharge(
          ControlStopCharge(&_servo, &_fet, &_current, &_chargeTimer)),
      _controlPowerOnDrone(
          ControlPowerOnDrone(&_servo, &_fet, &_current, &_chargeTimer)),
      _checkServoCurrent(CheckServoCurrent(&_servo, &_fet, &_current)) {}

/**
 * @brief Destroy the Servo Controller:: Servo Controller object
 *
 */
ChargeController::~ChargeController() {}

/**
 * @brief 処理を停止する
 *
 */
void ChargeController::stop(void) {
  _controlStartCharge.stop();
  _controlStopCharge.stop();
  _controlPowerOnDrone.stop();
}

/**
 * @brief 充電を開始する
 *
 */
void ChargeController::startCharge(void) {
  stop();
  _controlStartCharge.start();
}

/**
 * @brief 充電を開始する
 *
 * @param catchCnt 捕獲繰り返し回数
 * @param retryCnt USB接続するまでの動作をリトライする回数
 */
void ChargeController::startCharge(uint8_t catchCnt, uint8_t retryCnt) {
  stop();
  _controlStartCharge.start(catchCnt, retryCnt);
}

/**
 * @brief 充電開始処理中かどうか
 *
 * @return true
 * @return false
 */
bool ChargeController::isStartChargeExecuting(void) {
  return _controlStartCharge.isExecuting();
}

/**
 * @brief 充電を停止する
 *
 */
void ChargeController::stopCharge(void) {
  stop();
  _controlStopCharge.start();
}

/**
 * @brief 充電終了処理中かどうか
 *
 * @return true
 * @return false
 */
bool ChargeController::isStopChargeExecuting(void) {
  return _controlStopCharge.isExecuting();
}

/**
 * @brief ドローンの電源をONにする
 *
 */
void ChargeController::powerOnDrone(void) {
  stop();
  _controlPowerOnDrone.start();
}

/**
 * @brief ドローンの起動処理中かどうか
 *
 * @return true
 * @return false
 */
bool ChargeController::isPowerOnExecuting(void) {
  return _controlPowerOnDrone.isExecuting();
}

/**
 * @brief WASDでサーボの角度を微調整する
 *
 * @param input キーボード入力
 */
void ChargeController::wasdControl(char input) { _servo.wasdControl(input); }

/**
 * @brief 充電中かどうか
 *
 * @return true 充電中
 * @return false 充電中でない
 */
bool ChargeController::isCharging(void) {
  return _servo.isCatchDrone() && _servo.isConnectUsb() && _fet.read();
}

/**
 * @brief 初期位置かどうか
 *
 * @return true 初期位置
 * @return false 初期位置でない
 */
bool ChargeController::isInitPos(void) {
  return _servo.isReleaseDrone() && _servo.isDisconnectUsb() && !_fet.read();
}

/**
 * @brief 充電時間をミリ秒で取得する
 *
 * @return uint32_t 充電時間[ms]
 */
uint32_t ChargeController::getChargeTimeMillis(void) {
  return _chargeTimer.getTime();
}

/**
 * @brief 充電時間を取得する[sec]
 *
 * @return float 充電時間[sec]
 */
float ChargeController::getChargeTimeSec(void) {
  return float(_chargeTimer.getTime()) / 1000;
}

/**
 * @brief ドローンをキャッチしているかどうか
 *
 * @return true
 * @return false
 */
bool ChargeController::isCatchDrone(void) { return _servo.isCatchDrone(); }

/**
 * @brief ドローンをリリースしているかどうか
 *
 * @return true
 * @return false
 */
bool ChargeController::isReleaseDrone(void) { return _servo.isReleaseDrone(); }

/**
 * @brief USBを接続しているかどうか
 *
 * @return true
 * @return false
 */
bool ChargeController::isConnectUsb(void) { return _servo.isConnectUsb(); }

/**
 * @brief USBを切断しているかどうか
 *
 * @return true
 * @return false
 */
bool ChargeController::isDisconnectUsb(void) {
  return _servo.isDisconnectUsb();
}

/**
 * @brief サーボモータの指示値が目標角度に到達したかどうか
 *
 * @return true
 * @return false
 */
bool ChargeController::isTargetAngle(void) { return _servo.isTargetAngle(); }

/**
 * @brief 電流値を取得する
 *
 * @return float 電流値[mA]
 */
float ChargeController::getCurrent(void) { return _current.getCurrent(); }

/**
 * @brief 充電中の電流かどうか
 *
 * @return true 充電中である
 * @return false
 */
bool ChargeController::isChargingCurrent(void) {
  return getCurrent() >= CHARGE_CURRENT_CHARGING_THREASHOLD;
}

/**
 * @brief 満充電かどうか
 *
 * @return true 満充電である
 * @return false
 */
bool ChargeController::isFullCharge(void) {
  return isCharging() && isChargingCurrent() &&
         getCurrent() < CHARGE_CURRENT_STOP_THREASHOLD &&
         getChargeTimeMillis() > 30000;
}

/**
 * @brief アームをリリースすべきかどうか
 *
 * @return true
 * @return false
 */
bool ChargeController::haveToRelease(void) {
  return isCharging() && !isChargingCurrent() && getChargeTimeMillis() > 60000;
}

/**
 * @brief ループ処理
 *
 */
void ChargeController::loop(void) {
  static bool requestedStopCharge = false;
  _current.loop();
  if (!requestedStopCharge && isFullCharge()) {
    // 満充電になったら止める
    logger.info(
        "ChargeController.loop(): Stop charging due to full charge. current "
        "= " +
        String(_current.getCurrent()));
    stopCharge();
    requestedStopCharge = true;
  } else if (!requestedStopCharge && haveToRelease()) {
    // 充電開始したが電流が流れなかった場合
    logger.info(
        "ChargeController.loop(): Stop charging due to no current. current = " +
        String(_current.getCurrent()));
    stopCharge();
    requestedStopCharge = true;
  } else if (requestedStopCharge && !isFullCharge()) {
    requestedStopCharge = false;
  }

  // サーボ電流監視
  if (_checkServoCurrent.haveToEmargencyStopServo()) {
    _controlStartCharge.stop();
    _controlStopCharge.stop();
    _controlPowerOnDrone.stop();
  }

  if (_controlStartCharge.loop()) {
    logger.info("ChargeController.loop(): Finish to start charge");
  }
  if (_controlStopCharge.loop()) {
    logger.info("ChargeController.loop(): Finish to stop charge");
  }
  if (_controlPowerOnDrone.loop()) {
    logger.info("ChargeController.loop(): Finish to power on Tello");
  }
  if (_checkServoCurrent.loop()) {
    logger.info("ChargeController.loop(): Finish to check servo current");
  }
  _servo.loop();
}

/**
 * @brief サーボ角度の文字列を取得する
 *
 * @return String サーボ角度の文字列
 */
String ChargeController::toString(void) { return _servo.toString(); }

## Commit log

2023-03-25 [lib] Add submodule ArduinoCommon
2023-03-25 [doc][memo] Add submodule ArduinoCommon
2023-03-25 [eagle] Add schematic
    [tello-charger.brd, tello-charger.sch]
2023-03-26 [eagle] Update schematic
    [tello-charger.brd, tello-charger.sch]
2023-03-26 [doc][design] Add schematic and pcb layout
2023-03-26 [submodule] Update ArduinoCommon
2023-03-26 [TelloCharger] Change to use ServoESP32 of ArduinoCommon
2023-04-14 [src] Add MOSFET control
2023-04-14 [eagle] Add PDF of schematic and board
2023-05-06 [TelloCharger] Add ChargeController and FETController
2023-05-06 [TelloCharger] Add ChargeManager
2023-05-06 [TelloCharger] Add charge time for api response
2023-05-14 [TelloCharger] Add retry charge
2023-05-15 [TelloCharger] Add charger status
2023-05-16 [doc] Change API specification of power on
2023-05-16 [TelloCharger] Change power on api
2023-08-18 [TelloCharger] Update ArduinoCommon library
2023-08-18 [TelloCharger] Change power on time to 2sec from 1sec
2023-09-23 [TelloCharger] Add reading current
2023-09-23 [TelloCharger] Add auto stop charging by current
2023-10-08 [TelloCharger] Add fixed IP setting
    [main.cpp]
2023-10-08 [TelloCharger] Fixed start charge process with no current
2023-10-08 [TelloCharger] Adjust current threashold
2023-11-18 [TelloCharger] Check servo motor current
2023-11-18 [TelloCharger] Refactoring of charging controller
2023-11-22 [TelloCharger] Add logic to detect overcurrent and stop servo motor
2023-11-22 [Tello Charger] Change default position of arm
2025-04-26 fix: update MY_FIXED_IP_4 value
    ssid_example.hのMY_FIXED_IP_4の値を12から110に変更しました。
2025-05-02 [Arduino Common] Update ArduinoCommon
2025-05-02 fix: update subproject commit reference in ArduinoCommon
    ArduinoCommonのサブプロジェクトのコミット参照を78eceb7から95d029cに更新しました。
2025-05-02 fix: update subproject commit reference in ArduinoCommon
    ArduinoCommonのサブプロジェクトのコミットリファレンスを更新しました。
2025-05-02 fix: remove timestamp from payload examples in mqtt_interface.md
    mqtt_interface.mdのペイロード例からtimestampフィールドを削除しました。
2025-05-02 feat: enhance charge controller and add message builder
    - platformio.ini: 環境設定を整理し、依存ライブラリを更新
    - ChargeController.cpp: 充電時間を秒単位で取得するメソッドを追加し、不要なピン定義を削除
    - ChargeController.h: 充電時間を秒で取得するメソッドの宣言を追加
    - CurrentReader.cpp: I2C通信の初期化を修正し、ログ出力を追加
    - MessageBuilder.cpp: 充電状態をJSON形式で生成する関数を追加
    - MessageBuilder.h: JSON生成関数の宣言を追加
    - main.cpp: WiFi接続用のタスクを作成し、MQTTクライアントの初期化を追加
    - pinConfig.h: ピン設定を整理し、M5Stackの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
    [ChargeController.cpp, CurrentReader.cpp, main.cpp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]
2025-05-02 fix: update charging time retrieval in HttpServer
    HttpServer.cppの_onChargeGetメソッドで、充電時間の取得をミリ秒から秒に変更しました。
2025-05-03 fix: update subproject commit reference in ArduinoCommon ArduinoCommonのサブプロジェクトのコミット参照を更新しました。
2025-05-03 feat: implement DroneCharger MQTT protocol and message handling
    新しいファイル DroneChargerProtocol.cpp と DroneChargerProtocol.h を追加し、充電状態やリクエスト・レスポンスの構造体を定義しました。また、MQTT メッセージの送受信を管理する MqttHandler クラスを実装しました。MessageBuilder 関連の古いファイルを削除し、main.cpp での MQTT ハンドラの初期化を追加しました。
2025-05-03 feat: update platformio.ini and main.cpp for improved configuration
    platformio.iniの[env:m5stack-atom]および[env:m5stack-atoms3]セクションで、build_flagsを共通の設定から拡張するように変更しました。また、main.cppから不要なArduino.hのインクルードを削除し、M5Unified.hのインクルードを整理しました。さらに、taskWifi関数内のvTaskDelayの位置を調整しました。tel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
2025-05-03 fix: update subproject commit reference in ArduinoCommon
    ArduinoCommonのサブプロジェクトのコミット参照を更新しました。
